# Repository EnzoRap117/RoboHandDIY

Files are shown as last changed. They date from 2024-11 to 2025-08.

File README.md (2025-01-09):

RoboHandDIY is an ESP32-based robotic arm which uses LucidGloves as its mode of tracking finger position data. ESPNOW is used for wireless communication between the glove and arm. Presently, the arm can replicate forearm rotation, wrist flexion, and finger movements. 

This project uses LucidGloves prototype 4.1 running on a modified version of the code. Other than using LucidGloves as its mode of finger tracking, this project is not associated with LucidVR. 

<b>Information about and instructions for building the handtracking device can be found on the LucidVR github page:</b>
https://github.com/LucidVR/lucidgloves

<b>Official LucidVR website:</b> https://hackaday.io/project/178243-lucidgloves-vr-haptic-gloves-on-a-budget

______________________________________________________________

<b>RoboHandDIY Hardware:</b>

STL files for 3D printing the robotic hand are located in the hardware folder. All parts are designed to be able to print on an A1 mini. It is recommended that you print the palm model and coupler mount using supports.
Joint pegs should be printed with an aligned seam so it can be easily trimmed off for smooth rotation at the joints. If there is a version of a model marked with "_1" at the end, use that instead. It is recommended that you use the .3mf file if it is provided. The materials to build the LucidGlove are not included in this list, please refer to the LucidGloves github for more infromation.

<b>For building one stationary hand, you will need:</b>
* 5x MG90S micro-servo motors
* 1x MG996R servo motor
* 1x ESP32 uPesy Wroom Devkit
* 4x M2 screws
* 5x M2.5 screws
* 1x 5V power adapter (a 12 watt iPhone charger power adapter is recommended)
* 2x 5V rechargeable batteries
* 2x micro-USB wires (.25-.5m meters or less)
* 10m nylon thread
  
<i>(3d printed)</i>
* 1x palm (left or right)
* 15x finger segments (each finger segment differs slightly)
* 14x standard pegs
* 12x peg caps
* 1x IMR connector peg
* 1x wristoServo peg
* 1x wrist plate
* 1x wrist cover
* 4x 60mm servo arms
* 2x Long 60mm servo arms
* <i>(optionally)</i> 1x testMountingPlate

<b>If you are building an arm including the forearm and elbow joints, you will additionally need:</b>
* 1x 5*7cm prototyping perf board
* 1x MG996 servo motor
* 8x M5 screws
  
<i>(3d printed)</i>
* 1x upper coupler
* 1x lower coupler
* 1x coupler mount
* 1x main ring
* 1x servo base
* 2x large standoffs
* 2x small standoffs
* <i>(unfinished)</i> 1x bottom plate
 
<b>If you are building the forearm battery mount, you will need:</b>
* 4x M2 screws
* 1m of velcro strip
* 1x battery holder body
* 1x battery holder lid
* 150x80mm of soft foam (recommended to use the lid to create an outline)

______________________________________________________________
<b> RoboHandDIY software </b>

The code for the tracking glove and the robotic hand can be found in the software folder. You first need to run the "Addresser" program on the robot arm's ESP32 to determine its MAC address before attempting to connect it to the glove; running the "Addresser" program on the ESP32 will make it print its MAC address to Serial. Once the address is
obtained, use it to replace to template MAC adress in the "_main" file of the "lucidgloves-firmware_custom" sketch.

Each of the boards will continously run while powered. The robot arm should be powered before the glove is connected to power. Whenever the glove is connected to power, the fingers must be calibrated by forming a fist shape in order to stop the fingers on the robotic arm from jittering.
It might take several tries to get the fingers to calibrate correctly, this issue is not yet resolved.

______________________________________________________________
<b> Wiring and Power </b>

* Each of the ESP32 boards can be powered by a 5V rechargable battery with a cable connected directly to the mirco-USB port. The micro-servos should be powered by a separate 5V power adapter with a connection to the between the ground pin of the ESP32 and the ground wire of the leading to the adapter.
* If you are using the uPesy ESP32 Wroom 38pin board, it is recommended you use the pins which are already being used in the reciever code for the servo signal wires.
* Jumper wires can be used to connect the servo and board if female header pins are soldered to the board, but it is a tight fit.

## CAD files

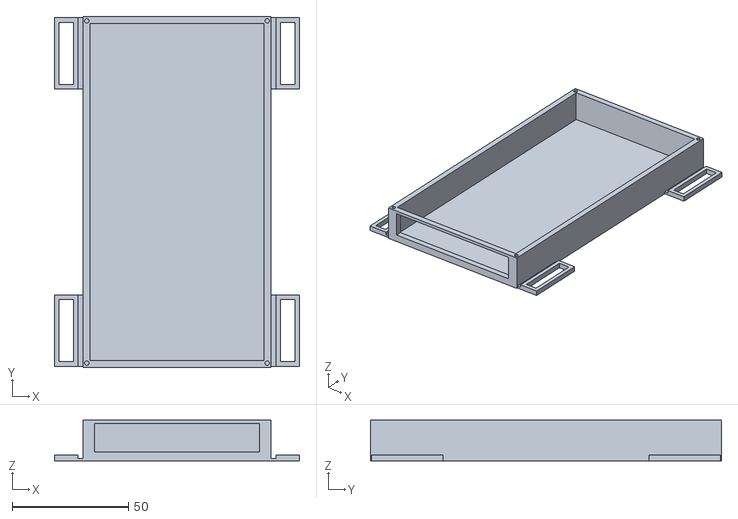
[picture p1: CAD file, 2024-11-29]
Hardware/forearmBattery/BatteryHolder_main.stl
105.3 x 151.0 x 17.5

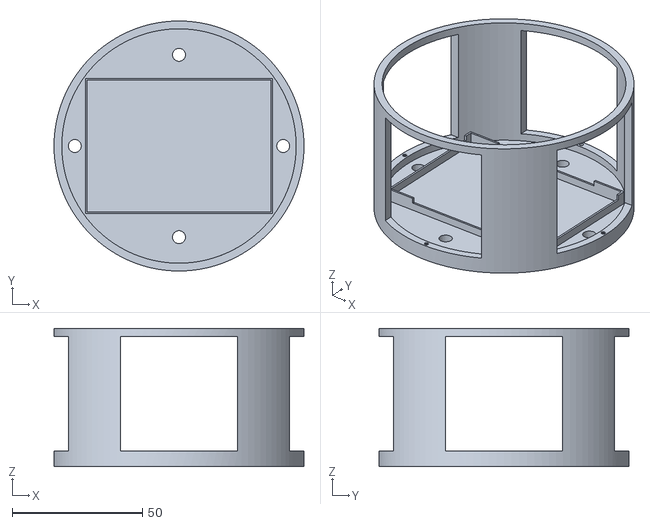
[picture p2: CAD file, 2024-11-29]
Hardware/forearmToElbowCoupler/mainRing.stl
96.0 x 96.0 x 53.0

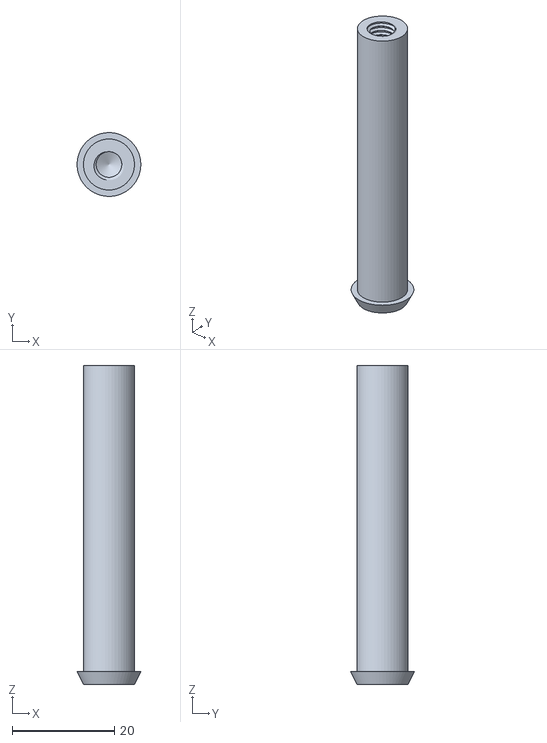
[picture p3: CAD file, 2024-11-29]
Hardware/connectorPegs/IMRConnectionPeg.stl
12.5 x 12.5 x 62.5

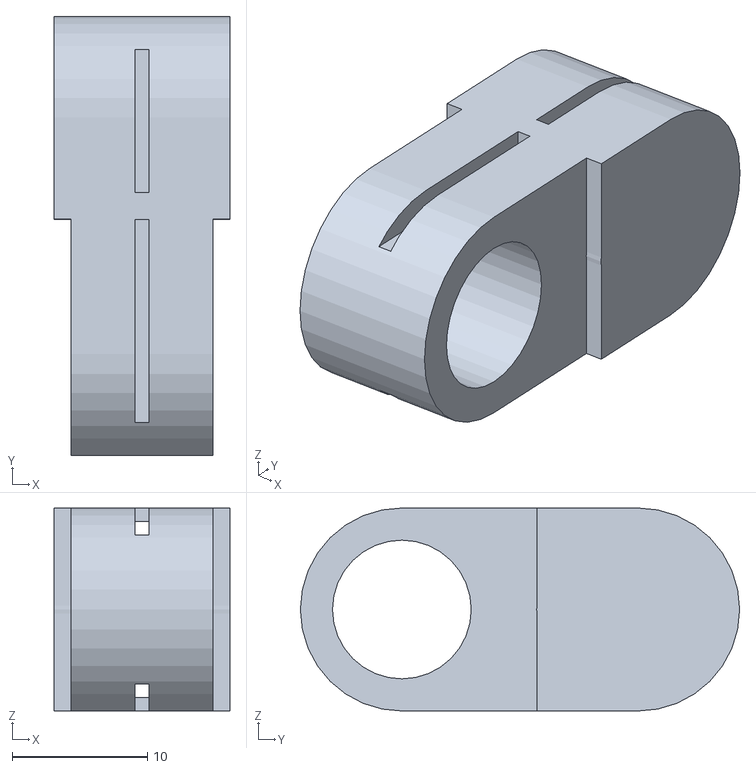
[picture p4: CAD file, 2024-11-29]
Hardware/fingers/Index/I3.stl
13.0 x 32.5 x 15.0

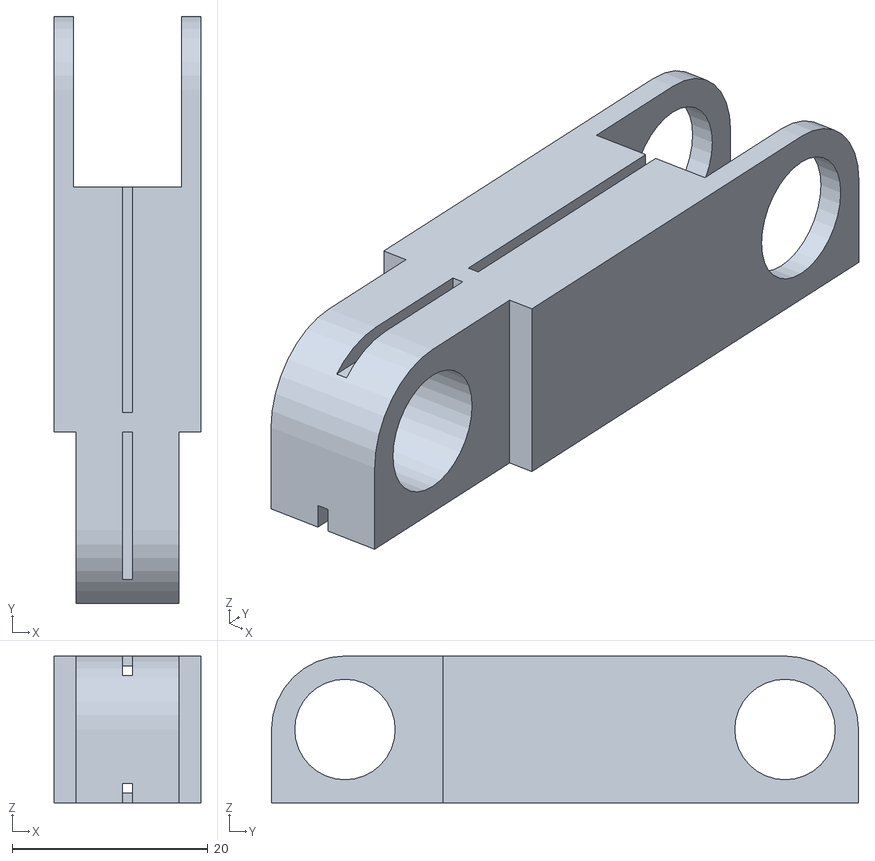
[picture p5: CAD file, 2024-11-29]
Hardware/fingers/Ring/R1_1.stl
15.0 x 59.9 x 15.0

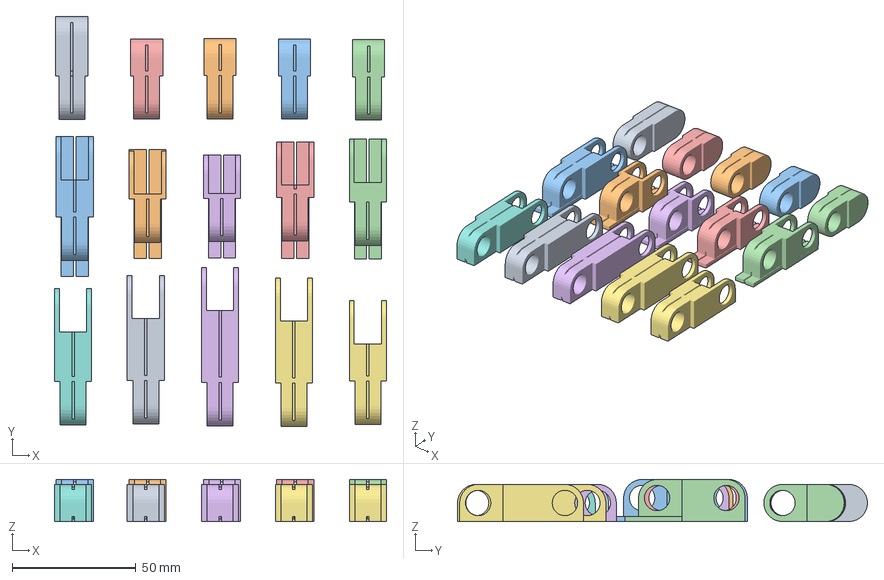
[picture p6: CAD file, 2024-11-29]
Hardware/fingers/RobotHand_FingerTray.3mf
134.0 x 165.5 x 17.0 mm
I1.stl
I3.stl x 4
M1.stl
P1.stl
T1.stl
T3.stl
I2_1.stl
T2_1.stl
M2_1.stl
R2_1.stl
P2_1.stl
R1_1.stl

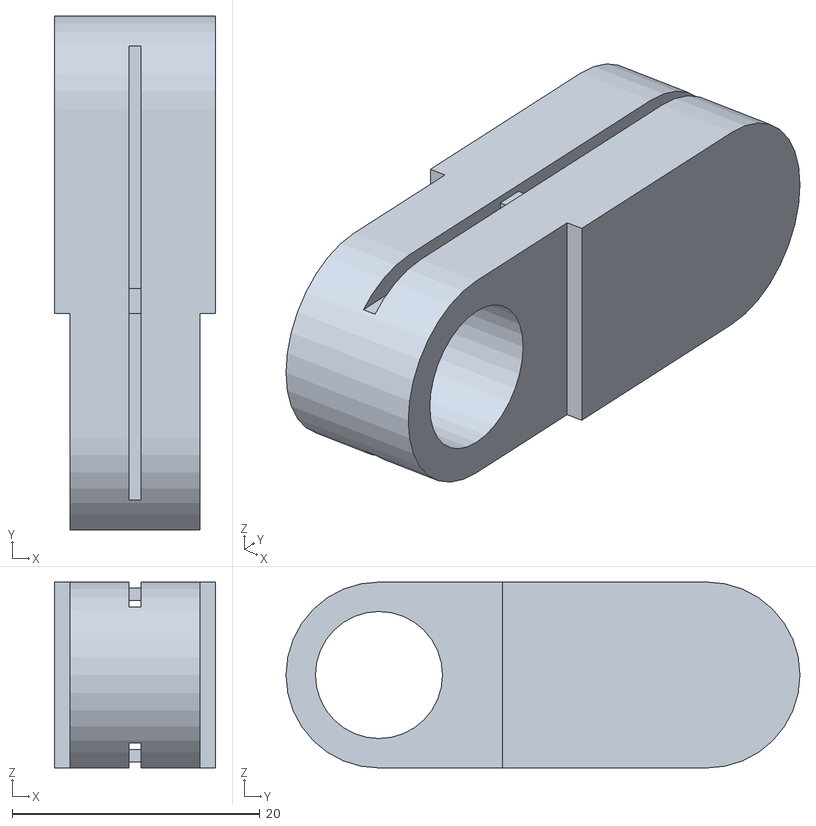
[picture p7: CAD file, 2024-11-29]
Hardware/fingers/Thumb/T3.stl
13.0 x 41.5 x 15.0

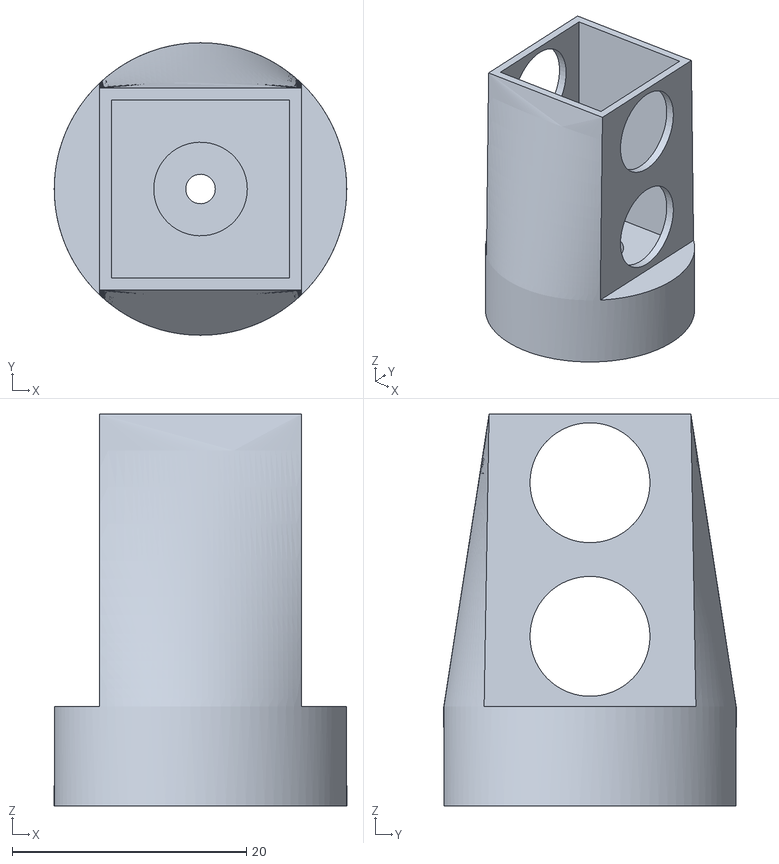
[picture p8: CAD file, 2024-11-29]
Hardware/forearmToElbowCoupler/upperCouplerShort.stl
25.0 x 25.0 x 33.5

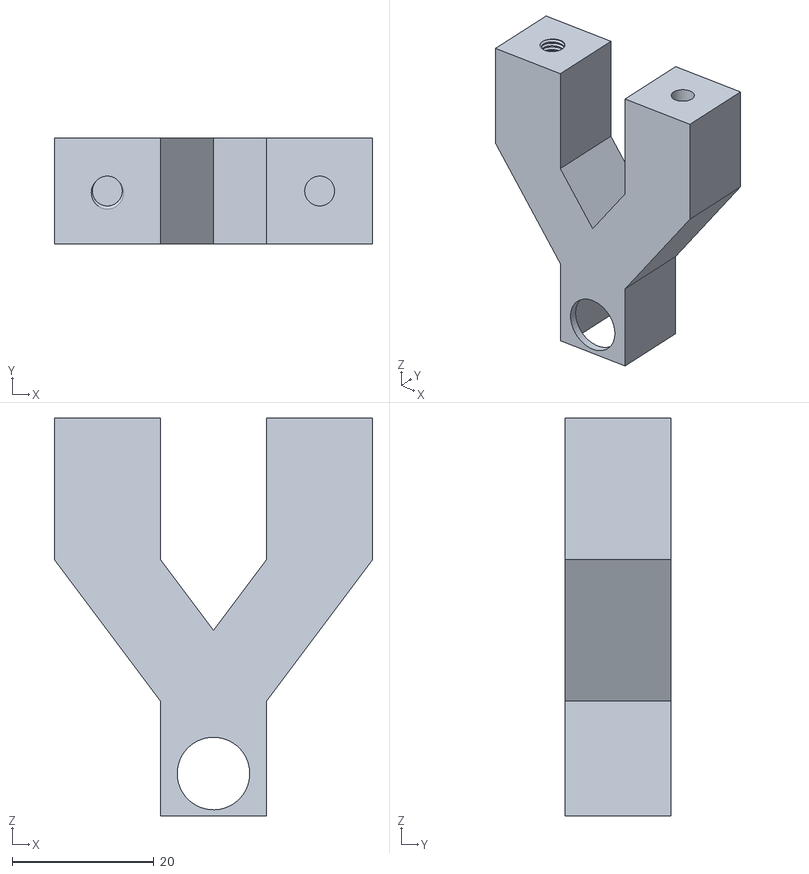
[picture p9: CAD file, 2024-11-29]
Hardware/forearmTruss/trussFork.stl
45.0 x 15.0 x 56.2

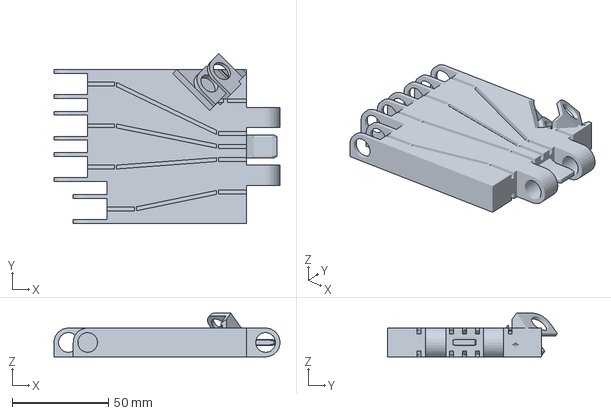
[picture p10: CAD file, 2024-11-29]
Hardware/palm/rightPalm.3mf
117.5 x 88.3 x 22.8 mm

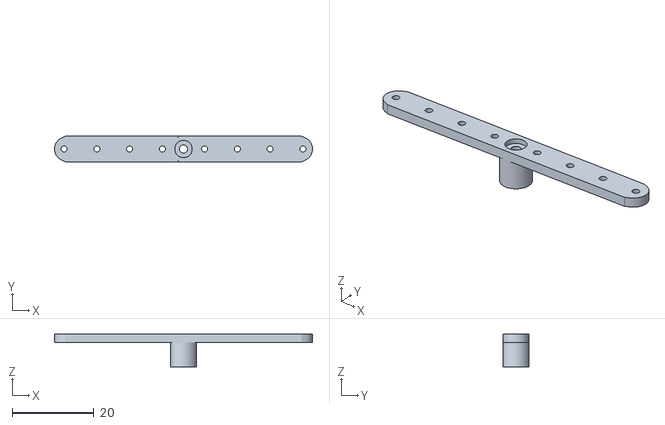
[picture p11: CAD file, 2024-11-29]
Hardware/Servo/CustomServoArm_60mm_Long.stl
63.0 x 6.30 x 8.00

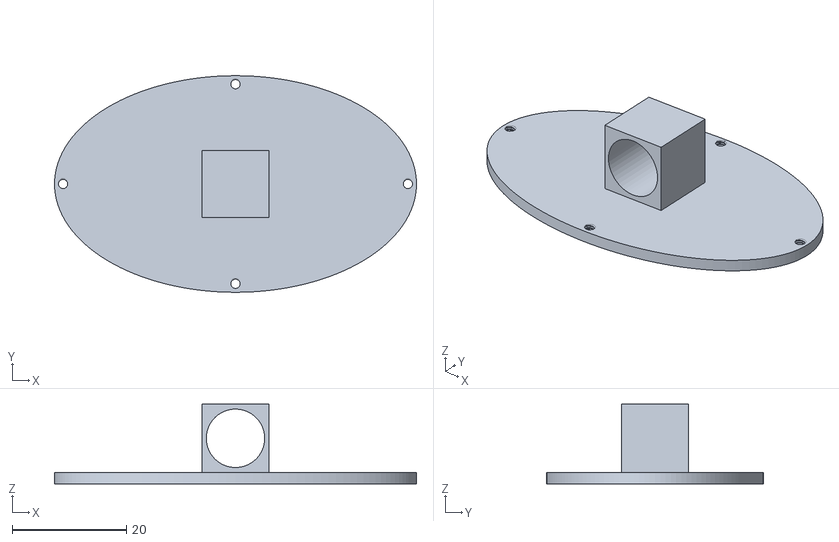
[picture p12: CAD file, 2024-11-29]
Hardware/testMountingPlate.stl
63.5 x 38.0 x 14.0

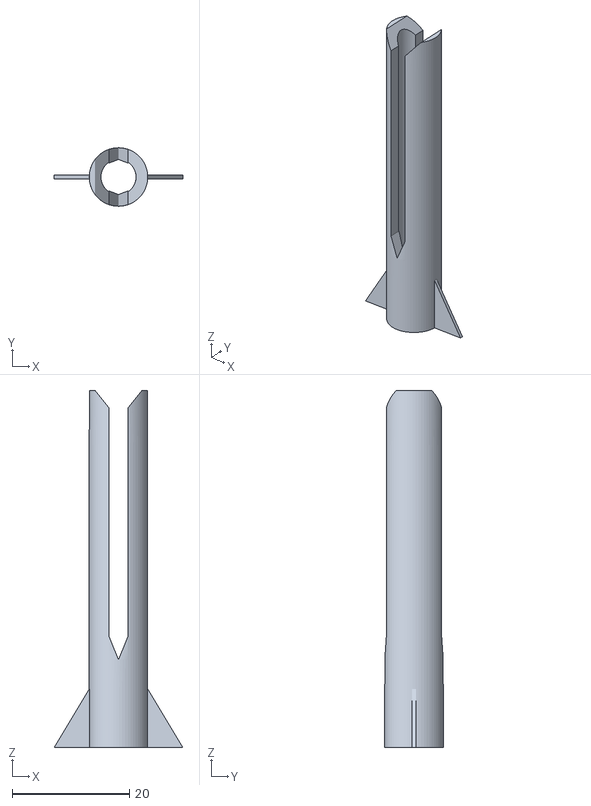
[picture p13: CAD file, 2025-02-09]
Hardware/Wrist/wristToServoJoint_V.2_fins v4.stl
22.0 x 10.0 x 61.0

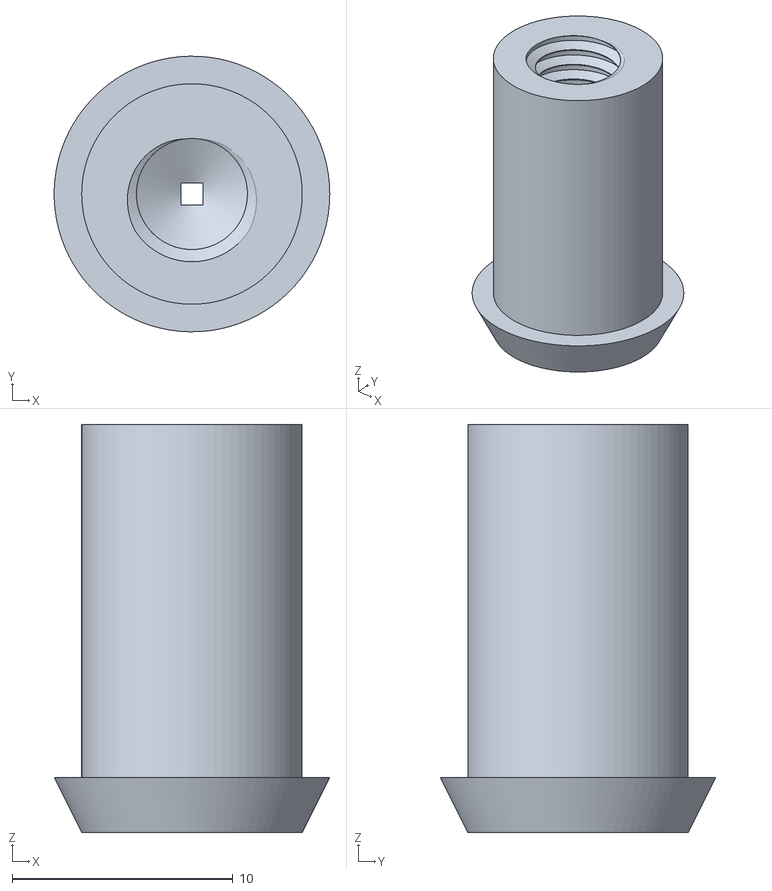
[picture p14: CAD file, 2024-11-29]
Hardware/connectorPegs/standardConnectorPeg.stl
12.5 x 12.5 x 18.5

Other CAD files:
Hardware/fingers/Pinky/P3.stl
Hardware/fingers/Index/I2_1.stl
Hardware/fingers/Middle/M2.stl
Hardware/fingers/Pinky/P2.stl
Hardware/Servo/CustomServoArm_60mm.stl
Hardware/Wrist/WristCover.stl
Hardware/Wrist/wristPlate.stl
Hardware/Wrist/wristToServoJoint.stl
Hardware/connectorPegs/screwCap.stl
Hardware/fingers/Index/I1.stl
Hardware/fingers/Index/I2.stl
Hardware/fingers/Middle/M1.stl
Hardware/fingers/Middle/M2_1.stl
Hardware/fingers/Middle/M3.stl
Hardware/fingers/Pinky/P1.stl
Hardware/fingers/Pinky/P2_1.stl
Hardware/fingers/Ring/R1.stl
Hardware/fingers/Ring/R2.stl
Hardware/fingers/Ring/R2_1.stl
Hardware/fingers/Ring/R3.stl
Hardware/fingers/Thumb/T1.stl
Hardware/fingers/Thumb/T2.stl
Hardware/fingers/Thumb/T2_1.stl
Hardware/forearmBattery/BatteryHolder_lid.stl
Hardware/forearmToElbowCoupler/CouplerMount.stl
Hardware/forearmToElbowCoupler/forearmToElbowConnector v18.f3d
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

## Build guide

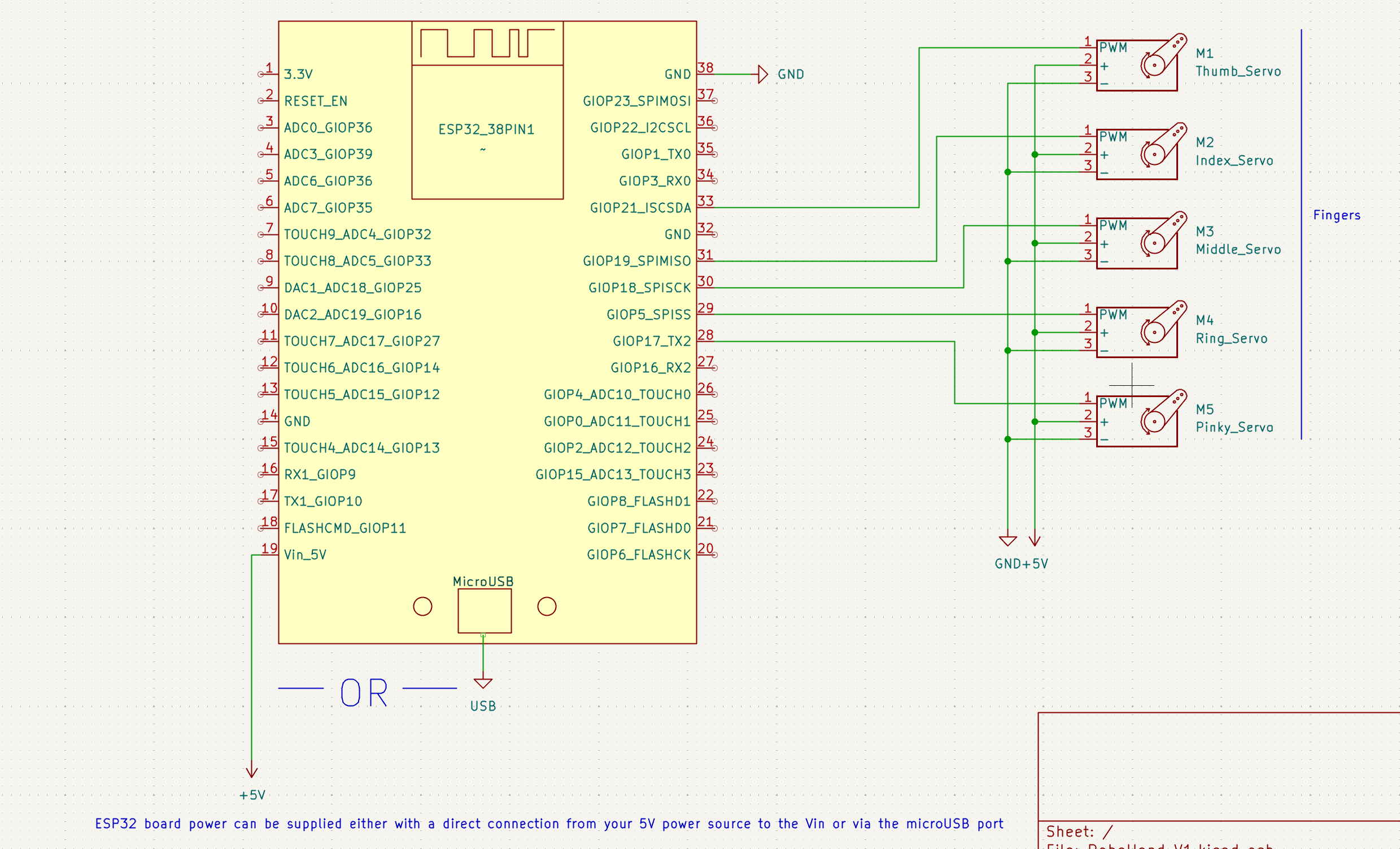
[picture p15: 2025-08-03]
RoboHandDIY V1 Wiring Schematic.png

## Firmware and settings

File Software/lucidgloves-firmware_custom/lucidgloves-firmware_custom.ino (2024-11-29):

/*
 * LucidGloves Firmware Version 4
 * Author: Lucas_VRTech - LucidVR
 * lucidvrtech.com
 */

#include "AdvancedConfig.h"
#include <esp_now.h>
#include <WiFi.h>

//This is the configuration file, main structure in _main.ino
//CONFIGURATION SETTINGS:
#define COMMUNICATION COMM_SERIAL //Which communication protocol to use
//serial over USB
  #define SERIAL_BAUD_RATE 115200
  
//serial over Bluetooth
  #define BTSERIAL_DEVICE_NAME "lucidgloves-left"

//ANALOG INPUT CONFIG
#define FLIP_POTS  true  //Flip values from potentiometers (for fingers!) if they are backwards

//Gesture enables, make false to use button override
#define TRIGGER_GESTURE true
#define GRAB_GESTURE    true
#define PINCH_GESTURE   true


//BUTTON INVERT
//If a button registers as pressed when not and vice versa (eg. using normally-closed switches),
//you can invert their behaviour here by setting their line to true.
//If unsure, set to false
#define INVERT_A false
#define INVERT_B false
#define INVERT_JOY false
#define INVERT_MENU false
#define INVERT_CALIB false
//These only apply with gesture button override:
#define INVERT_TRIGGER false
#define INVERT_GRAB false
#define INVERT_PINCH false


//joystick configuration
#define JOYSTICK_BLANK true //make true if not using the joystick
#define JOY_FLIP_X false
#define JOY_FLIP_Y false
#define JOYSTICK_DEADZONE 10 //deadzone in the joystick to prevent drift (in percent)

#define NO_THUMB false //If for some reason you don't want to track the thumb

#define USING_CALIB_PIN true //When PIN_CALIB is shorted (or it's button pushed) it will reset calibration if this is on.

#define USING_FORCE_FEEDBACK false //Force feedback haptics allow you to feel the solid objects you hold
#define SERVO_SCALING false //dynamic scaling of servo motors

#if defined(ESP32)
  //(This configuration is for ESP32 DOIT V1 so make sure to change if you're on another board)
  #define PIN_PINKY     36
  #define PIN_RING      39
  #define PIN_MIDDLE    34
  #define PIN_INDEX     35
  #define PIN_THUMB     32
  #define PIN_WRIST     33
  #define PIN_FOREARM   25
  #define PIN_ELBOW
  #define PIN_JOY_X     20
  #define PIN_JOY_Y     25
  #define PIN_JOY_BTN   26
  #define PIN_A_BTN     20 
  #define PIN_B_BTN     14
  #define PIN_TRIG_BTN  12 //unused if gesture set
  #define PIN_GRAB_BTN  13 //unused if gesture set
  #define PIN_PNCH_BTN  23 //unused if gesture set
  #define PIN_CALIB      0 //button for recalibration (You can set this to GPIO0 to use the BOOT button, but only when using Bluetooth.)
  #define DEBUG_LED 2
  #define PIN_PINKY_MOTOR    5  //used for force feedback
  #define PIN_RING_MOTOR      18 //^
  #define PIN_MIDDLE_MOTOR    19 //^
  #define PIN_INDEX_MOTOR     21 //^
  #define PIN_THUMB_MOTOR     17 //^
  #define PIN_MENU_BTN        27
  
//PINS CONFIGURATION 
#elif defined(__AVR__)
  //(This configuration is for Arduino Nano so make sure to change if you're on another board)
  #define PIN_PINKY     A0
  #define PIN_RING      A1
  #define PIN_MIDDLE    A2
  #define PIN_INDEX     A3
  #define PIN_THUMB     A4
  #define PIN_JOY_X     A6
  #define PIN_JOY_Y     A7
  #define PIN_JOY_BTN   7 
  #define PIN_A_BTN     8 
  #define PIN_B_BTN     9
  #define PIN_TRIG_BTN  10 //unused if gesture set
  #define PIN_GRAB_BTN  11 //unused if gesture set
  #define PIN_PNCH_BTN  12 //unused if gesture set
  #define PIN_CALIB     13 //button for recalibration
  #define DEBUG_LED     LED_BUILTIN
  #define PIN_PINKY_MOTOR     2 //used for force feedback
  #define PIN_RING_MOTOR      3 //^
  #define PIN_MIDDLE_MOTOR    4 //^
  #define PIN_INDEX_MOTOR     5 //^
  #define PIN_THUMB_MOTOR     6 //^
  #define PIN_MENU_BTN        8
#endif


//Test ------------------------------------------------

void OnDataSent(const uint8_t *mac_addr, esp_now_send_status_t status);


/*
#define ALWAYS_CALIBRATING CALIBRATION_LOOPS == -1

#define CALIB_OVERRIDE true
#if USING_CALIB_PIN && COMMUNICATION == COMM_SERIAL && PIN_CALIB == 0 && !CALIB_OVERRIDE
  #error "You can't set your calibration pin to 0 over usb. You can calibrate with the BOOT button when using bluetooth only. Set CalibOverride to true to override this."
#endif

//ESPNOW Necessary Items
  #include <esp_now.h>
  #include <WiFi.h>

  //Sheild address
  uint8_t broadcastAddress[] = {0x24, 0xdc, 0xc3, 0x43, 0xc4, 0x98};

  // Structure example to send data
  // Must match the receiver structure
  typedef struct struct_message {
    char a[32];
    char* GloveData;
  } struct_message;

  // Create a struct_message called myData
  struct_message myData;

  esp_now_peer_info_t peerInfo;


  void OnDataSent(const uint8_t *mac_addr, esp_now_send_status_t status) {
    Serial.print("\r\nLast Packet Send Status:\t");
    Serial.println(status == ESP_NOW_SEND_SUCCESS ? "Delivery Success" : "Delivery Fail");
  }


// --- ESPNOW Setup end ---

//ICommunication* comm;
int loops = 0;
void setup() {
  //EPSNOW
  // Init Serial Monitor
  Serial.begin(115200);

  // Set device as a Wi-Fi Station
  WiFi.mode(WIFI_STA);

  // Init ESP-NOW
  if (esp_now_init() != ESP_OK) {
     Serial.println("Error initializing ESP-NOW");
     return;
  }

  // Once ESPNow is successfully Init, we will register for Send CB to
  // get the status of Trasnmitted packet
  esp_now_register_send_cb(OnDataSent);
  
  // Register peer
  memcpy(peerInfo.peer_addr, broadcastAddress, 6);
  peerInfo.channel = 0;  
  peerInfo.encrypt = false;
  
  // Add peer        
  if (esp_now_add_peer(&peerInfo) != ESP_OK){
    Serial.println("Failed to add peer");
     return;
  }

  //LUCID Code
  #if COMMUNICATION == COMM_SERIAL
    comm = new SerialCommunication();
  #elif COMMUNICATION == COMM_BTSERIAL
    comm = new BTSerialCommunication();
  #endif  
  comm->start();

  setupInputs();

  #if USING_FORCE_FEEDBACK
    setupServoHaptics();  
  #endif
  
}

void loop() {

  if (comm->isOpen()){
    #if USING_CALIB_PIN
    bool calibButton = getButton(PIN_CALIB) != INVERT_CALIB;
    if (calibButton)
      loops = 0;
    #else
    bool calibButton = false;
    #endif
    
    bool calibrate = false;
    if (loops < CALIBRATION_LOOPS || ALWAYS_CALIBRATING){
      calibrate = true;
      loops++;
    }
    
    int* fingerPos = getFingerPositions(calibrate, calibButton);
    
    

    bool joyButton = getButton(PIN_JOY_BTN) != INVERT_JOY;

    #if TRIGGER_GESTURE
    bool triggerButton = triggerGesture(fingerPos);
    #else
    bool triggerButton = getButton(PIN_TRIG_BTN) != INVERT_TRIGGER;
    #endif

    bool aButton = getButton(PIN_A_BTN) != INVERT_A;
    bool bButton = getButton(PIN_B_BTN) != INVERT_B;

    #if GRAB_GESTURE
    bool grabButton = grabGesture(fingerPos);
    #else
    bool grabButton = getButton(PIN_GRAB_BTN) != INVERT_GRAB;
    #endif

    #if PINCH_GESTURE
    bool pinchButton = pinchGesture(fingerPos);
    #else
    bool pinchButton = getButton(PIN_PNCH_BTN) != INVERT_PINCH;
    #endif

    bool menuButton = getButton(PIN_MENU_BTN) != INVERT_MENU;


    //Atempting to send this ^^
    strcpy(myData.a, "LucidGlove data");
    myData.GloveData = encode(fingerPos, getJoyX(), getJoyY(), joyButton, triggerButton, aButton, bButton, grabButton, pinchButton, calibButton, menuButton);
    esp_err_t result = esp_now_send(broadcastAddress, (uint8_t *) &myData, sizeof(myData));

    
    if (result == ESP_OK) {
    Serial.println("Sent with success");
    }
    else {
      Serial.println("Error sending the data");
    }
    
    
    // --End of Send--
    
    comm->output(encode(fingerPos, getJoyX(), getJoyY(), joyButton, triggerButton, aButton, bButton, grabButton, pinchButton, calibButton, menuButton));

    #if USING_FORCE_FEEDBACK
      char received[100];
      if (comm->readData(received)){
        int hapticLimits[5];
        //This check is a temporary hack to fix an issue with haptics on v0.5 of the driver, will make it more snobby code later
        if(String(received).length() >= 10) {
           decodeData(received, hapticLimits);
           writeServoHaptics(hapticLimits); 
        }
      }
    #endif
    delay(LOOP_TIME);
  }
}
*/

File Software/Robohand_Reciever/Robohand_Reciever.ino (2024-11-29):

/*  This program requires a another board wired up to a lucidGlove
    running "lucidgloves-firmware_custom.ino"

    Refer to "One_Way_Comm_Test_RecieverForGlove" for more explanation
    as to how the data tranmission works
*/
#include <esp_now.h>
#include <WiFi.h>
#include "ESP32Servo.h"

 // create Servo object to control a servo
Servo pinkyServo;
Servo ringServo;
Servo middleServo;
Servo indexServo;
Servo thumbServo;
Servo wristServo;
Servo forearmServo;

Servo myServos[] = {thumbServo, indexServo, middleServo, ringServo, pinkyServo};
int len = 5;

//int potValues[5];
char letters[] = {'A', 'B', 'C', 'D', 'E'};

typedef struct struct_message {
    //char a[32];
    byte thumbVal;
    byte indexVal;
    byte middleVal;
    byte ringVal;
    byte pinkyVal;
    byte wristVal;
    byte forearmVal;
    //int GloveData[5];
} struct_message;

struct_message myData;

int val;

void OnDataRecv(const uint8_t * mac, const uint8_t *incomingData, int len) {
  memcpy(&myData, incomingData, sizeof(myData));
  /*
  for(int k = 0; k < 5; k++){
    Serial.print(letters[k]);
    Serial.print(": ");
    Serial.print(myData.GloveData[k]);
    Serial.print(" ");
  }
  Serial.println();
  */

  /*
  for(int i = 0; i < 5; i++){
    val = myData.GloveData[i];
    val = map(val, 0, 4095, 0, 180);
    Serial.print(letters[i]);
    Serial.print(": ");
    Serial.print(val);
    Serial.print(" ");
  }
  */
  Serial.println();
  moveServos();
}

void moveServos(){

  
  thumbServo.write(myData.thumbVal);

  indexServo.write(myData.indexVal);

  middleServo.write(myData.middleVal);

  ringServo.write(myData.ringVal);
 
  pinkyServo.write(myData.ringVal);

  wristServo.write(myData.wristVal);

  forearmServo.write(myData.forearmVal);
  
}

void setup() {
  pinkyServo.attach(19); //27
  ringServo.attach(18); //5
  middleServo.attach(5); //18
  indexServo.attach(17); //19
  thumbServo.attach(21);
  wristServo.attach(5);
  foreServo.attach(16);

  // Initialize Serial Monitor
  Serial.begin(115200);
  
  // Set device as a Wi-Fi Station
  WiFi.mode(WIFI_STA);

  // Init ESP-NOW
  if (esp_now_init() != ESP_OK) {
    Serial.println("Error initializing ESP-NOW");
    return;
  }
  
  // Once ESPNow is successfully Init, we will register for recv CB to
  // get recv packer info
  esp_now_register_recv_cb(esp_now_recv_cb_t(OnDataRecv));
}

void loop() {

}

  

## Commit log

2025-02-09 improved wristToServoJoint
    [wristToServoJoint_V.2_fins v4.stl]
2025-08-03 Added wiring schematic
